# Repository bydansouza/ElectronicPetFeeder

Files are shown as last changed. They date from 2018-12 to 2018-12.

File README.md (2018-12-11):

# About this! 
Electronic Pet Feeder Project - Automatic Feeder for Dogs and Cats ;)

By Daniel Henrique Camargo de Souza @ PIN22107 - IFSC/Electronic Engineering/Professors: Daniel Lohmann AND Robinson Pizzio - Dezembro/2018

# Descript:

This project consists of an electronic automatic feeder for dogs and cats, and this project were made from course Integrator Project class in undergraduate at Electronic Engineering by IFSC/Florianópolis@Brazil.

# Guide to using this repository folders and files
Here you find this structure of folders and files

* `CODE` contains the main code, the Makefile and includes for compile code to microcontroller ESP8266. 

* `ELECTRONIC_DESIGN` contains the files for electronic scheme and PCB design of the circuit for the control system.

* `MECHANICAL_DESIGN` contain the files of mechanical part, essentially the helicoid part design, other parts were made from commercials items.

* `_guides` contain files for learning about sensor and controllers used in this project, essentially datasheets and manuals

* `_models` contain files for other electronic pet feeder, but this was made with Arduino (sic) 

* `_patents` contain files of patents discovered about electronic pet feeders.

* `_refs` Others references files

# Steps for sucess:

* 1) Market research:

** First we proceded in a market research, seeking out a similar product. **

List of similar products:

   [10 Best Automatic Pet Feeders 2017](https://www.youtube.com/watch?v=MUnrIJn3qq8)

   [10 Best Automatic Pet Feeders 2018](https://www.youtube.com/watch?v=D8cHpOWlC1c)

   [JEMPET Petwant SmartFeeder Automatic Pet Feeder](http://www.petwant.com/)
    
   [Automatic Cat Feeder | PF-10 CAT](https://www.petfeedster.com/product/automatic-cat-feeder/)
        
** in following, we search the prices of these similar products **
    
   [JEMPET Petwant SmartFeeder Automatic Pet Feeder](https://www.amazon.com/Petwant-SmartFeeder-Automatic-Dispenser-Controlled/dp/B01GFTZPDQ)
    
   [Smart Feed Automatic Pet Feeder](https://store.petsafe.net/smart-feed)
    
   [Automatic Cat Feeder | PF-10 CAT](https://www.amazon.com/New-Pet-Feedster-PF-10-PLUS/dp/B01N9D4672)

* 2) Diferenciais Attributes for this project:

    All configs via MQTT
    
    Notification for user 
    
    Water control, Temperature and level

# Mechanical Project

This project is a prototype, then we use PVC commercial tubes of the 100mm to make mechanical part. however, for helicoidal transport of feed, we maked (via freecad) a design of the helicoid and built it via 3D printer. this part design you can see in folder `MECHANICAL_DESIGN`
    
We inspired from [Helidoid Model](https://www.thingiverse.com/thing:27854) to construct the helicoid part. This is inside into PVC tube of the 100mm of format "T". in the base of the helicoid have a motor that spin this helicoid liberating the feed.

The Helicoid design part coudl be seen in the next image. 
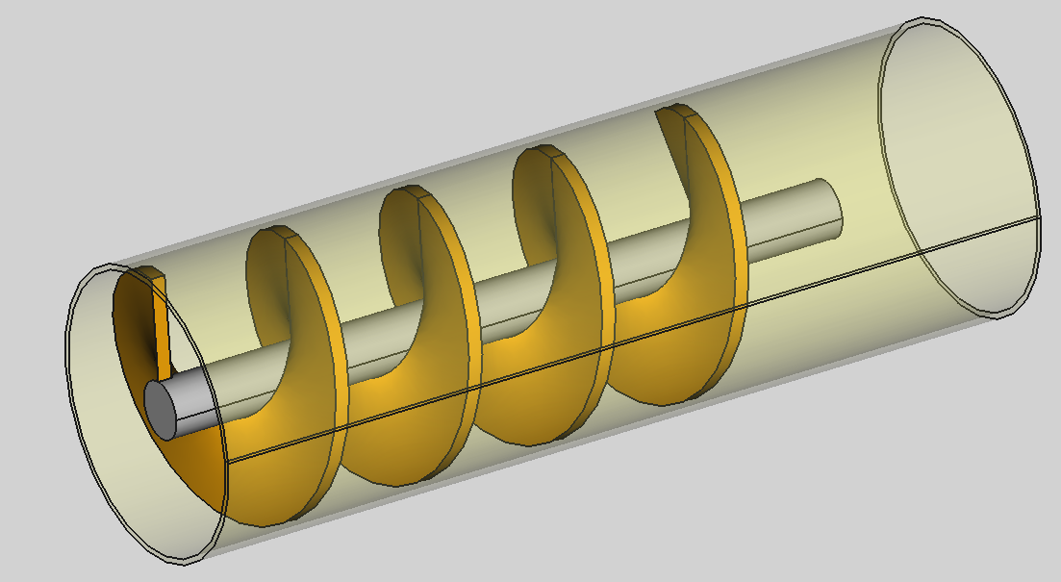
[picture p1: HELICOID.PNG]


The feed fall into the pot and under it (in the base) have a load cell for 2Kg, controlled from MCU (ESP8266). The client set, with MQTT commands, a quantity of feed and the system control the motor to spin the necessary to liberate a quantity seted.

In the base of system, have too another load cell, of the 50Kg, that monitoring the quantity of feed that fall into the pot (exited of system load). inside in code have a routine that calculate the variation of load, that fall into the pot and exited of system load, this two quantities should are equals.

For monitoring and control the water input and output, have been installed two solenoid valves. Inside the water pot have a temperature sensor and level sensor that through MCU controller we monitoring this two variables, and controled the start or stop of solenoids valves (if necessary).

# Electronic Project

Let's go to the part that interest us. For the control system, we used a microcontroller ESP8266 because it contain various periferics integrated, example is Wi-Fi Module.

Together of the MCU microcontroller, we used two accessories periferics. The first is HX711, Load cell controller that communicate with MCU part trough two pins serial interface, we implemented the librarie for this communicate with ESP8266 (see you into `CODE`). The second is RTC (Real Time Controller) based in DS1307, this is used in control of the time, and for this we used the librarie avaiable in `esp-open-rtos`

For the water temperature control, we used the DS18B20 Sensor (because this is water resistant), then for communicate with MCU microcontroller this sensor use one wire communication, and this is implemented in the librarie included in `esp-open-rtos`.

In the water level control, we used a capacitive sensor connected in input of 555 oscillator. according that the level rises, the oscillation produced in 555 change, the capacitive sensor controll the frequency of the oscillation in 555, thus we have a converter of the water level in frequency of oscilation. the second stage is connect the output os the 555 in an VCO (Voltage Control Oscilator) configured to convert frequency oscilations in voltages levels, thus we have the complete cicle, and we connect this output voltage level in an analog to digital converter of the MCU Controller.

The PCB design could be seen in the next image.  
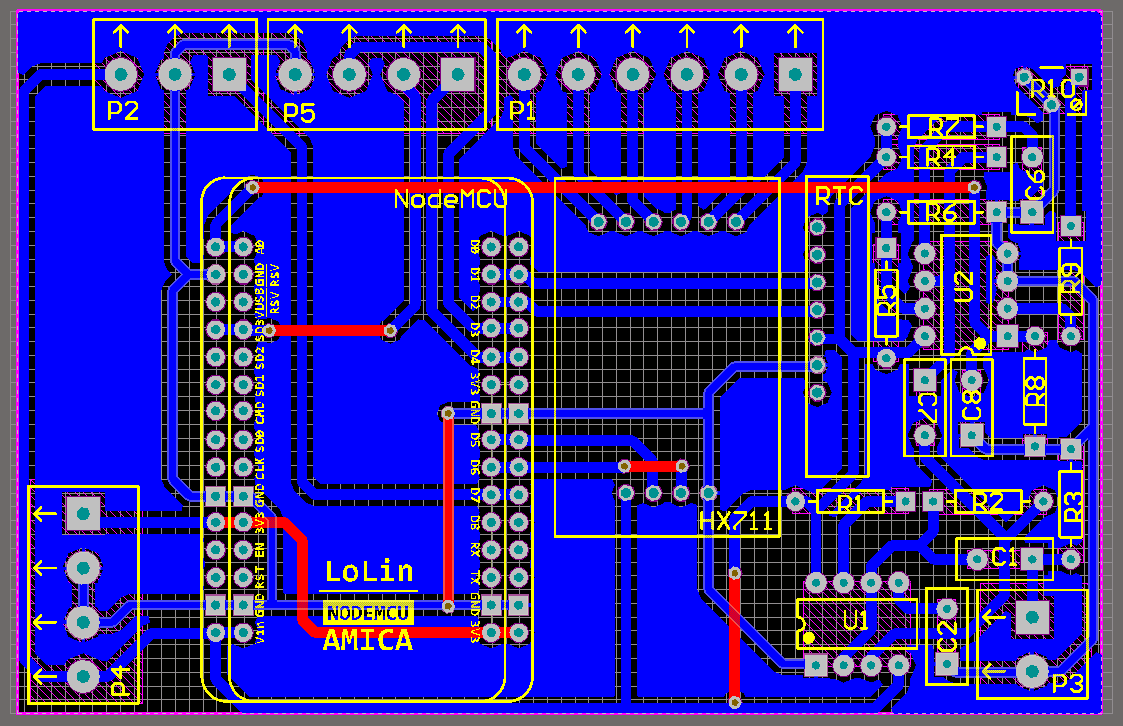
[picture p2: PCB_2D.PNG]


In this design we priorise the final dimension of board and the disposition os the components in board for reduce EMI an another other possibles mistakes.

The 3D PCB design could be seen in the next image. 
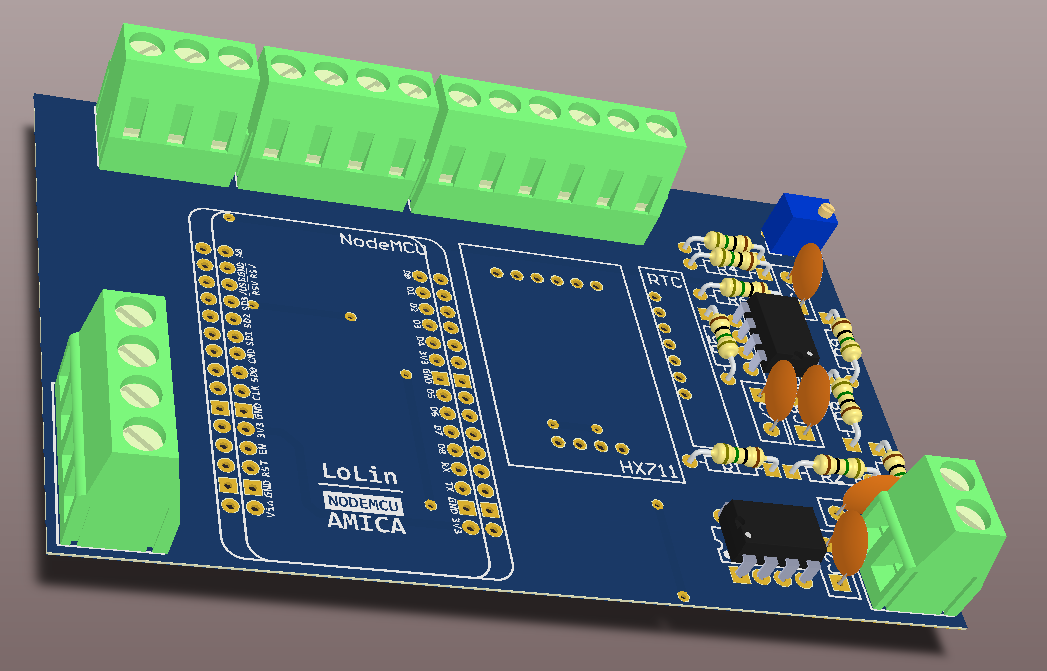
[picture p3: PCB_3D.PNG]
PCB 3D


## Main Code

The main code was made with esp-open-rtos sdk to ESP8266, then recommended to use the [esp-open-rtos](https://github.com/SuperHouse/esp-open-rtos). after defines, we created a sctruc that contain the principals control variables and the principals flags for control system, see next.

```
typedef struct {
	union
	{
		struct
		{
			uint32_t fIsTime		: 1;	//Chegou a Hora da Dose
			uint32_t fEqualDose		: 1;	//Dose Igualou
			uint32_t fMotorDose		: 1;	//Start/Stop do Motor da Dose
			uint32_t fWaterLevel	: 1;	//Chegou no Nível de Agua
			uint32_t fWaterTemp		: 1;	//Temperatura Ultrapassou
			uint32_t fWaterInput	: 1;	//Start/Stop entrada de agua
			uint32_t fWaterOutput	: 1;	//Start/Stop Saída de agua
			uint32_t fUnusedBits	: 25;	//Flags não usadas (fUnusedBits+Others = 32bits)
		};
		uint32_t fAllFlags;					//All Flags
	}			feeder_flags;			//Flags de Controle
	uint8_t 	feeder_nDose;			//Numero de Doses Diárias programadas
	uint32_t 	feeder_min[NMAX_DOSE];	//Minutos das Doses programadas
	uint32_t 	feeder_hour[NMAX_DOSE];	//Horas das Doses programadas
	uint32_t 	feeder_mday;			//Marca o Dia, para não repetir horários
	uint32_t 	feeder_dose;			//Quatidade da Dose Programada
	uint32_t	feeder_delay;			//Delay para as demais Tarefas
	float 		feeder_waterTemp;		//Temperatura da Agua permitida
}petFeederControl_t;
```
For the mensures and controls, we create 11 tasks, you can see theses tasks in the main code in `CODE` folder. for MQTT publisher and subscrtibe routines we was made based in code produced by @xtarke avaiable [Here](https://github.com/xtarke/kairos/tree/master/codes/mqtt). 

# Others Projects
[Pet Feeder w/ Arduino](https://www.instructables.com/id/Automatic-Arduino-Powered-Pet-Feeder/)

[IoT Pet Feeder](https://www.hackster.io/circuito-io-team/iot-pet-feeder-10a4f3)

[Other Pet Feeder](https://www.circuito.io/blog/automatic-pet-feeder/)

[Other Pet Feeder w/ Arduino](https://circuitdigest.com/microcontroller-projects/automatic-pet-feeder-using-arduino)

[Other Mechanical Pet Feeder](https://www.youtube.com/watch?v=hpQ21NZ_fuw)

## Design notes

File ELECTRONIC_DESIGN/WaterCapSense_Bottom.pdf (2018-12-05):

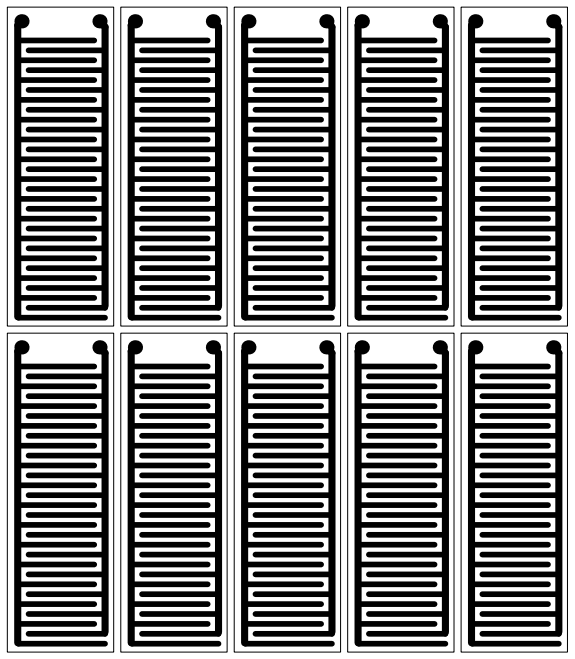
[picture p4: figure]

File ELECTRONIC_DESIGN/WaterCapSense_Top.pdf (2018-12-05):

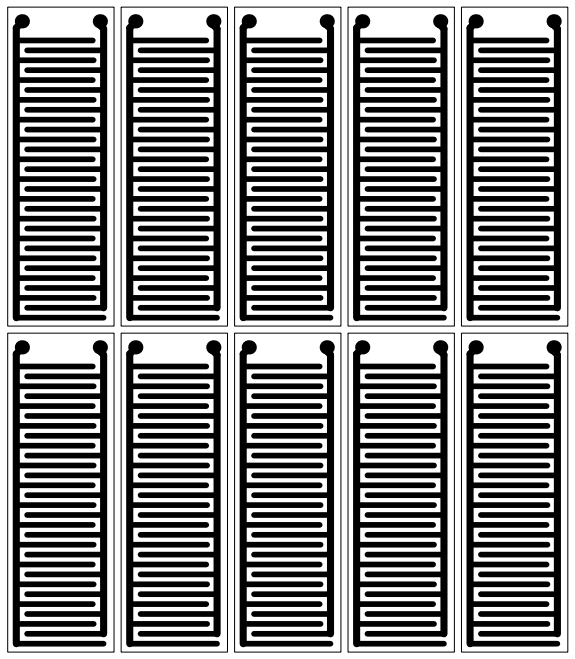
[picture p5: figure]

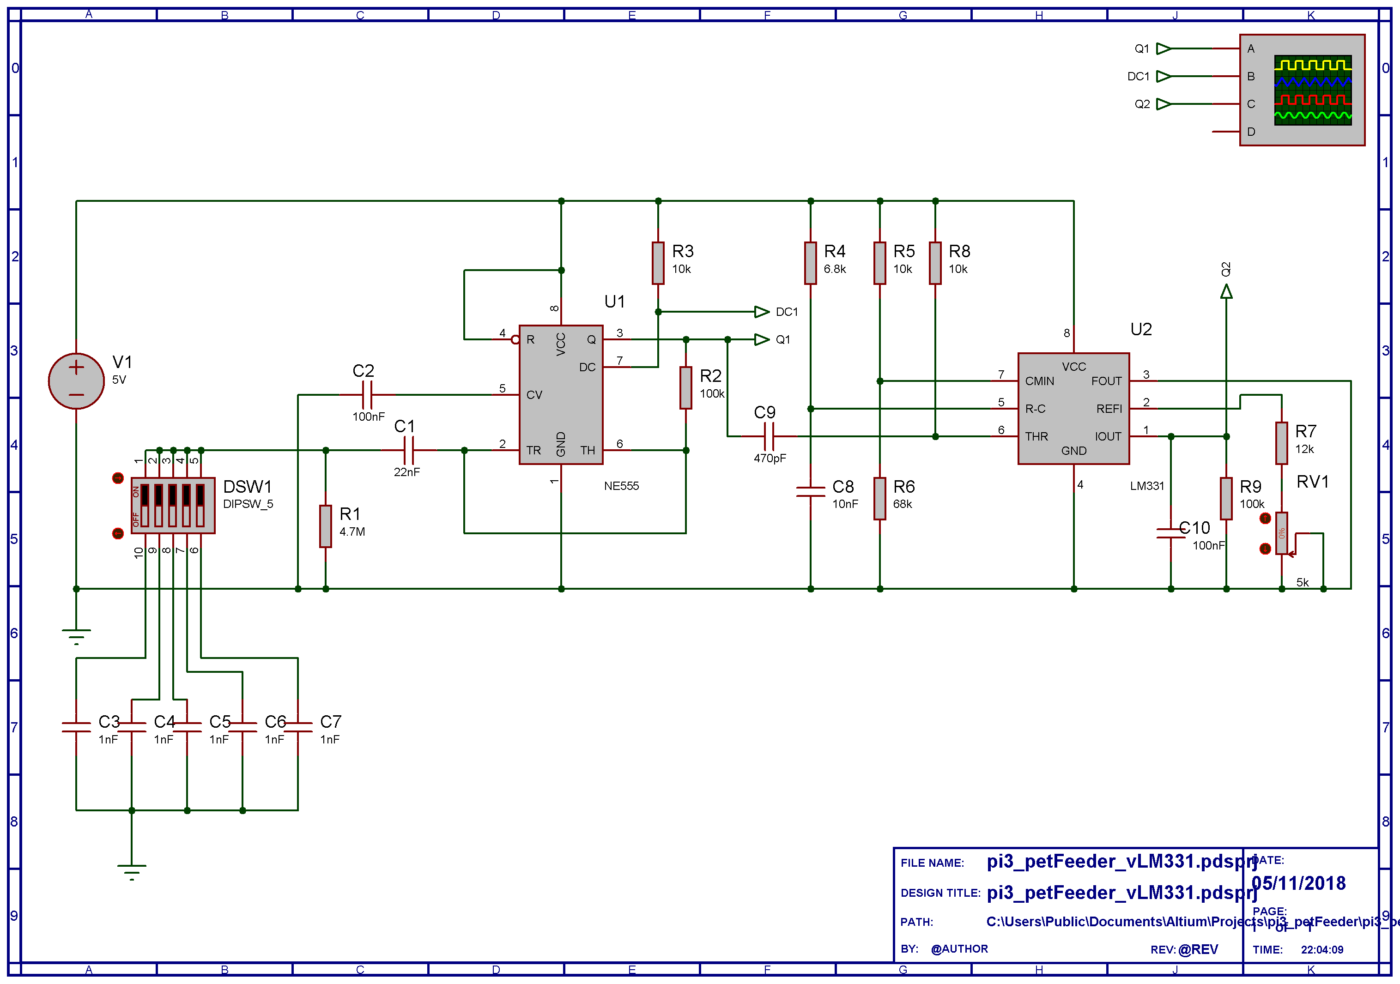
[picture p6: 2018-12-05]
ELECTRONIC_DESIGN/pi3_petFeeder_vLM331.png

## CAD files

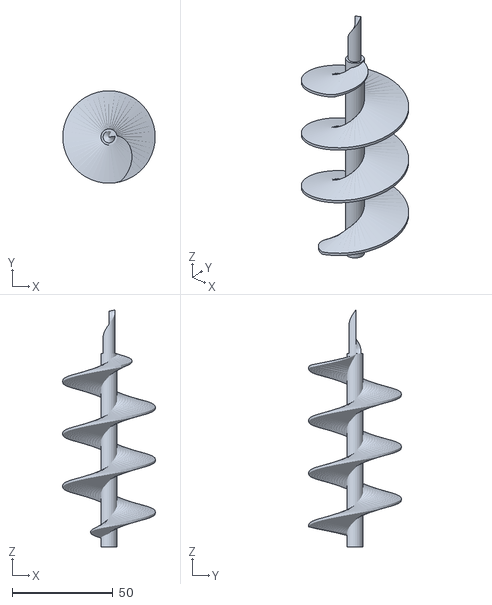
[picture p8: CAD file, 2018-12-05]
_models/Auger-based_Cat_Feeder/auger.stl
45.9 x 45.9 x 117.5

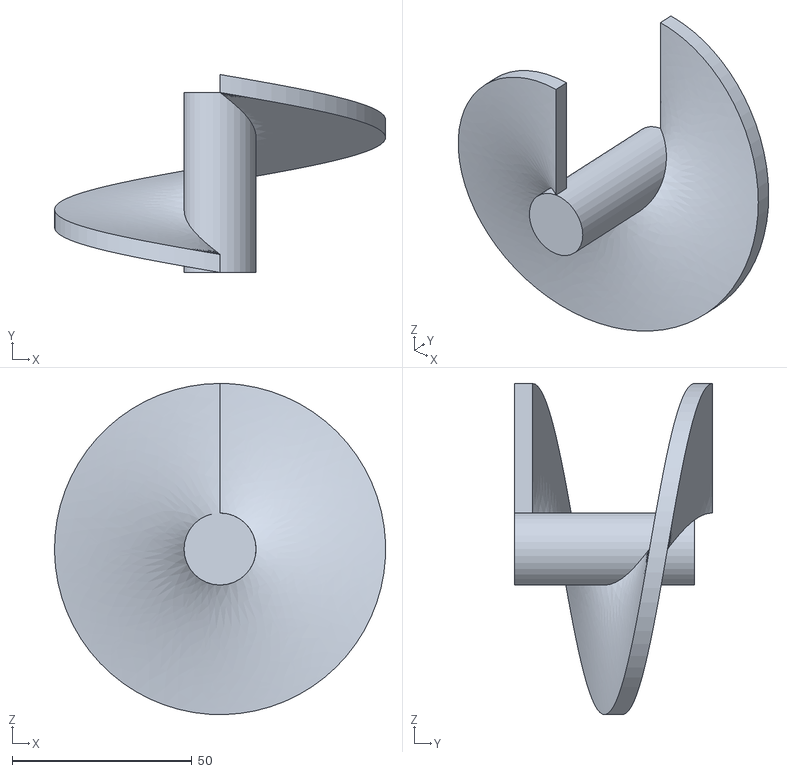
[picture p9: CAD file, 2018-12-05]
MECHANICAL_DESIGN/5x_helicoid_part001.stl
92.0 x 55.0 x 92.0

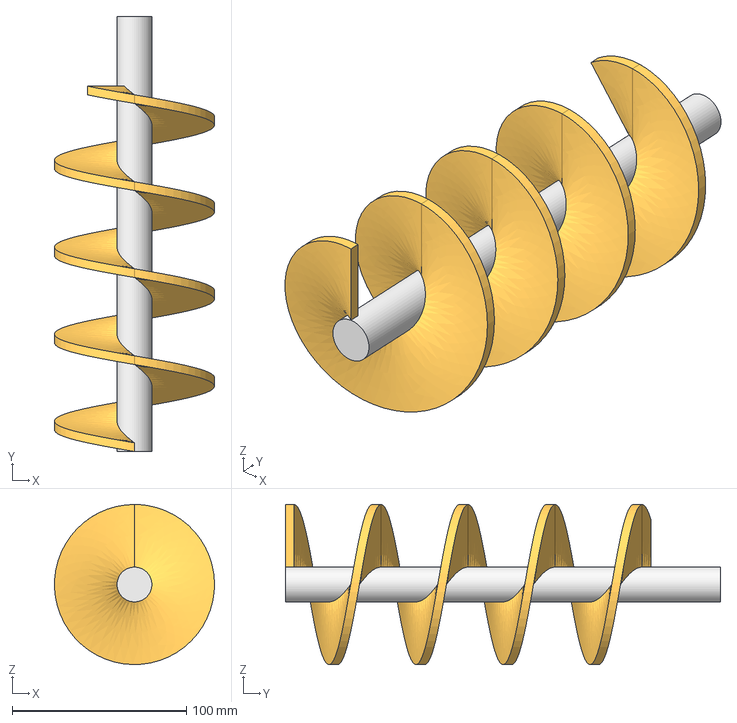
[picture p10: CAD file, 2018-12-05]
MECHANICAL_DESIGN/_helicoid.FCStd
91.9 x 250.0 x 92.0 mm
Eixo

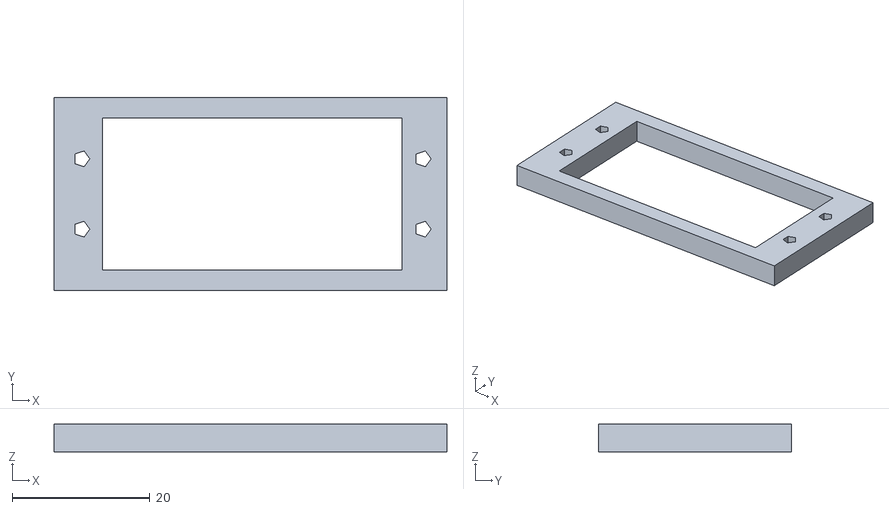
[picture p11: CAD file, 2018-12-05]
_models/Auger-based_Cat_Feeder/auger_servoshim.stl
57.0 x 28.0 x 4.00

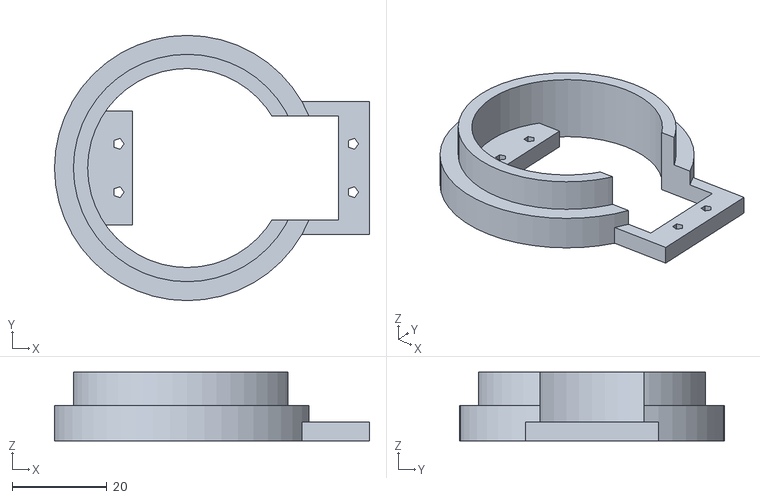
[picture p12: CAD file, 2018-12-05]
_models/Auger-based_Cat_Feeder/auger_tubemount.stl
66.5 x 56.0 x 14.5

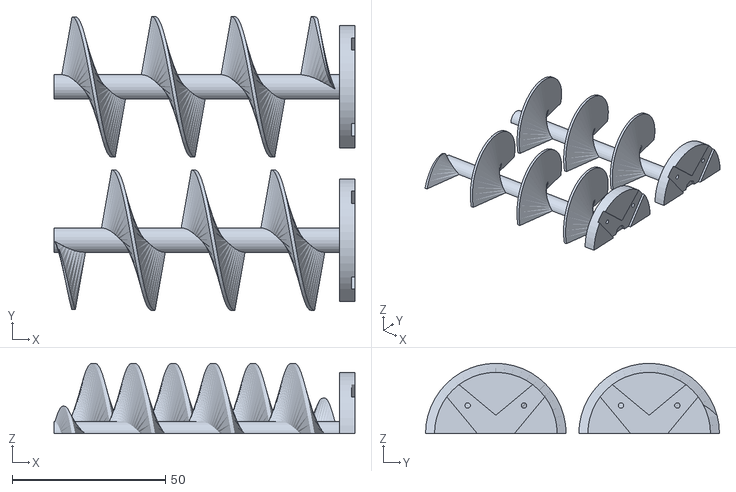
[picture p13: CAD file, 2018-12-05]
_models/Auger-based_Cat_Feeder/auger_screwplate.stl
98.0 x 95.9 x 22.9

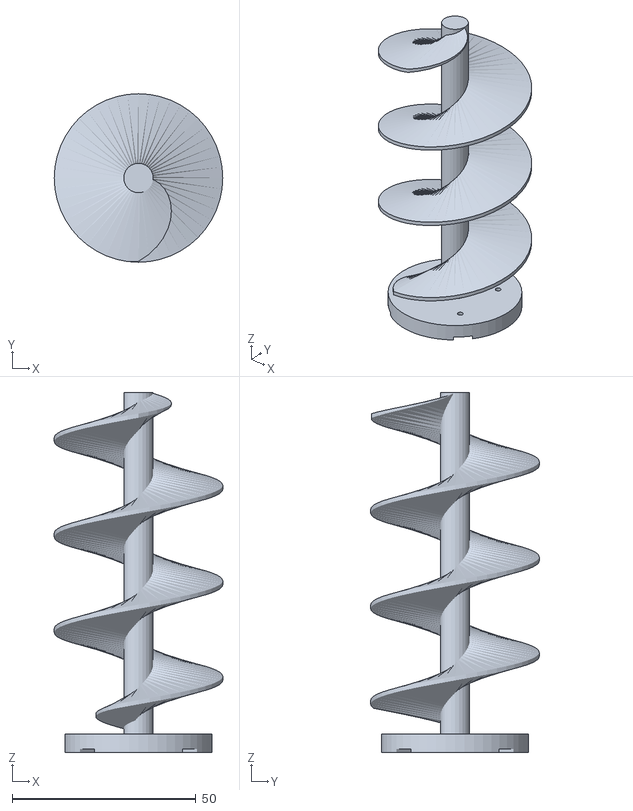
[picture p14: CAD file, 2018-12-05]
_models/Auger-based_Cat_Feeder/auger_screw.stl
45.9 x 45.9 x 98.0

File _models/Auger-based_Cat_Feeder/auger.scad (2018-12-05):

use <Thread_Library.scad>

// slice along Y-axis

*auger();
auger_import();

drivemount();

tubemount();

*servoshim();

%pvctube();

*servo();

module auger_import() {
    intersection() {
        translate([-45,-45,0]) cube(96);
        rotate([0,0,-15]) import("auger.stl");
    }
}
module auger() {
    cylinder(h=96, r=4, $fn=24);    
    trapezoidThread( 
        length=118,
        pitch=26,
        pitchRadius=8,
        threadHeightToPitch=0.70,
        profileRatio=0.20,
        threadAngle=10,
        RH=true,
        clearance=0.1,
        backlash=0.1,
        stepsPerTurn=48
    );
}

module drivemount() {
    translate([0,0,-2]) difference() {
        cylinder(h=5, r=40/2, $fn=48);
        for (angle = [0, 90, 180, 270]) translate([0,0,-1]) rotate([0,0,-45+angle]) {
            linear_extrude(height=2) polygon([[-8.5/2,0],[8.5/2,0],[8.5/2,8.5/2],[5.4/2,42/2],[-5.4/2,42/2],[-8.5/2,8.5/2]]);
            translate([13,0,0]) cylinder(h=8, r=0.9, $fn=12);  // 10 or 13
        }
        cylinder(h=2, r=3, $fn=8);
    }
}

module pvctube() {
    translate([0,0,-3]) difference() {
        cylinder(h=90, r=55/2, $fn=48);
        translate([0,0,-1]) cylinder(h=92, r=48/2, $fn=48);
    }
    // TODO: measure PVC tube and make sure these numbers make sense
}

module tubemount() {
    color([1,0,0])
    translate([0,0,-1-3]) difference() {
        union() {
            difference() {
                union() {
                    cylinder(h=3+5, r=48/2, $fn=48);
                    translate([0,0,-6.5]) cylinder(h=7.5, r=56/2, $fn=48);
                    translate([13,-22/2-3,-6.5]) cube([25.5,22+3*2,4]);
                }
                translate([0,0,-7]) cylinder(h=20, r=42/2, $fn=48);
                translate([0,-22/2,-19.5]) cube([32,22,20+10]);
            }
            translate([-21.5,-24/2,-6.5]) cube([10,24,4]);
        }
        translate([-4.5-10,-20.2/2,-11]) union() {
            translate([0,5,0]) cylinder(h=10, r=1.2);
            translate([0,5+10.2,0]) cylinder(h=10, r=1.2);
            translate([50.5-1,5,0]) cylinder(h=10, r=1.2);
            translate([50.5-1,5+10.2,0]) cylinder(h=10, r=1.2);
        }
    }
    // #2 x length? 2.0mm?  hole is ~1.55mm
}


module servoshim() {
    color([.7,.7,0])
    translate([0,0,-1-3-20]) difference() {
        union() {
            difference() {
                translate([-18.5,-22/2-3,-6.5]) cube([31.5+25.5,22+3*2,4]);
                translate([-18,-22/2,-19.5]) cube([18+32,22,20+10]);
            }
            translate([-18.5,-24/2,-6.5]) cube([7,24,4]);
        }
        translate([-4.5-10,-20.2/2,-11]) union() {
            translate([0,5,0]) cylinder(h=10, r=1.2);
            translate([0,5+10.2,0]) cylinder(h=10, r=1.2);
            translate([50.5-1,5,0]) cylinder(h=10, r=1.2);
            translate([50.5-1,5+10.2,0]) cylinder(h=10, r=1.2);
        }
    }
}




module servo() {
    color([0,0.7,.3])
    translate([-4.5-10,-20.2/2,-12-3]) union() {
        cube([50.5,20.2,4.5]);
        translate([4.5,0,0]) cube([41.5,20.2,11]);
        translate([4.5+10,20.2/2,11]) cylinder(h=4, r=3, $fn=24);
        translate([0+1,5,0]) cylinder(h=10, r=1);
        translate([0+1,5+10.2,0]) cylinder(h=10, r=1);
        translate([50.5-1,5,0]) cylinder(h=10, r=1);
        translate([50.5-1,5+10.2,0]) cylinder(h=10, r=1);
    }
}

// TODO: T-junction tube?  Or drill hole in top?
// TODO: diagonal mount to the bin?

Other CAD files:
MECHANICAL_DESIGN/_helicoid_part01.FCStd
_models/Auger-based_Cat_Feeder/augerslice.scad
_models/Auger-based_Cat_Feeder/Thread_Library.scad
MECHANICAL_DESIGN/helicoid.stl

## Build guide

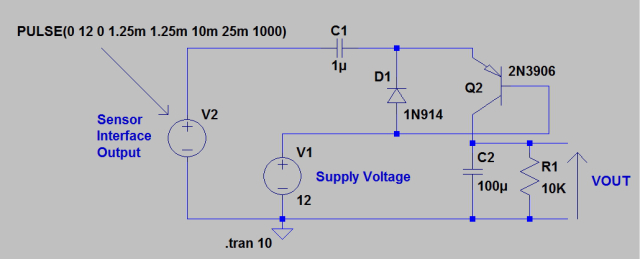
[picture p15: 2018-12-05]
_guides/waterLevelCapacitive/v2f.jpg

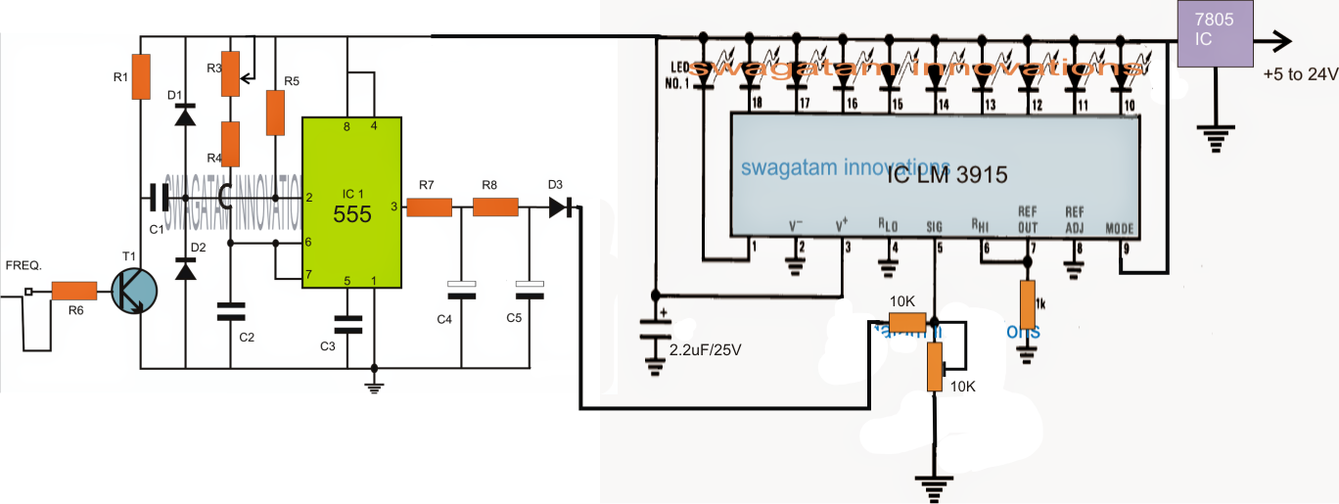
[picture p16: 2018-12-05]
_guides/waterLevelCapacitive/main-qimg-3cc157e7e807a82d9649140c95fcf219.png

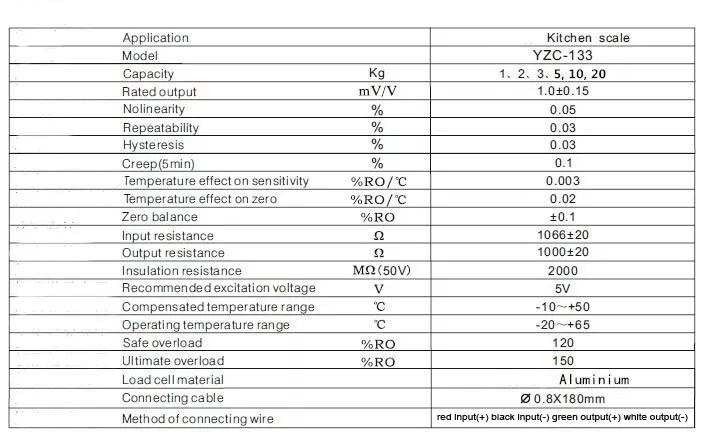
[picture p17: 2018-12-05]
_guides/hx711/celula-de-carga-2kg-sensor-de-peso-arduino-0213-D_NQ_NP_987008-MLB26000520462_092017-F.webp

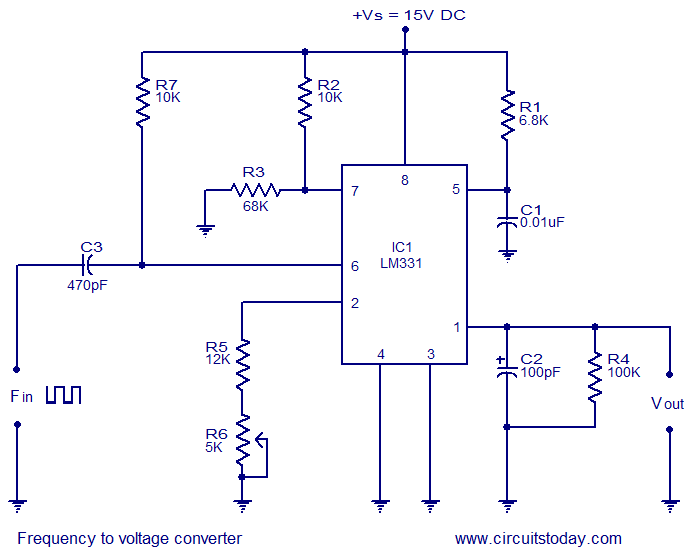
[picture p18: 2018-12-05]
_guides/waterLevelCapacitive/Frequency-to-Voltage-Converter.png

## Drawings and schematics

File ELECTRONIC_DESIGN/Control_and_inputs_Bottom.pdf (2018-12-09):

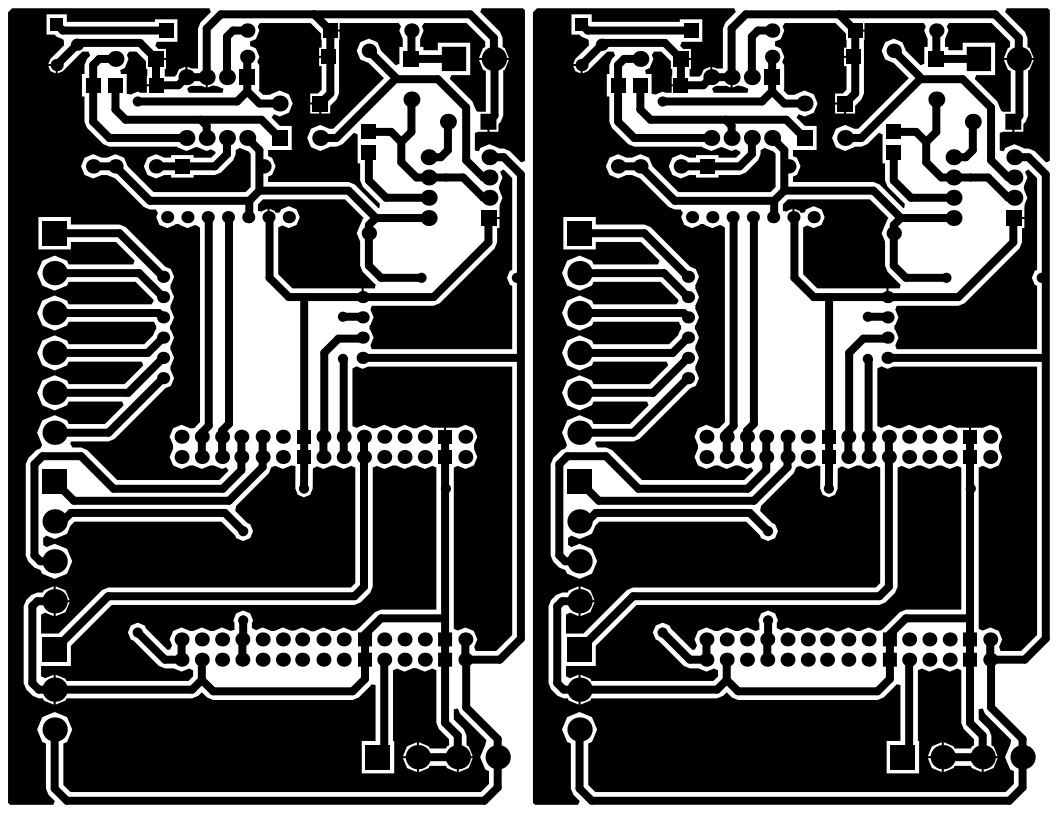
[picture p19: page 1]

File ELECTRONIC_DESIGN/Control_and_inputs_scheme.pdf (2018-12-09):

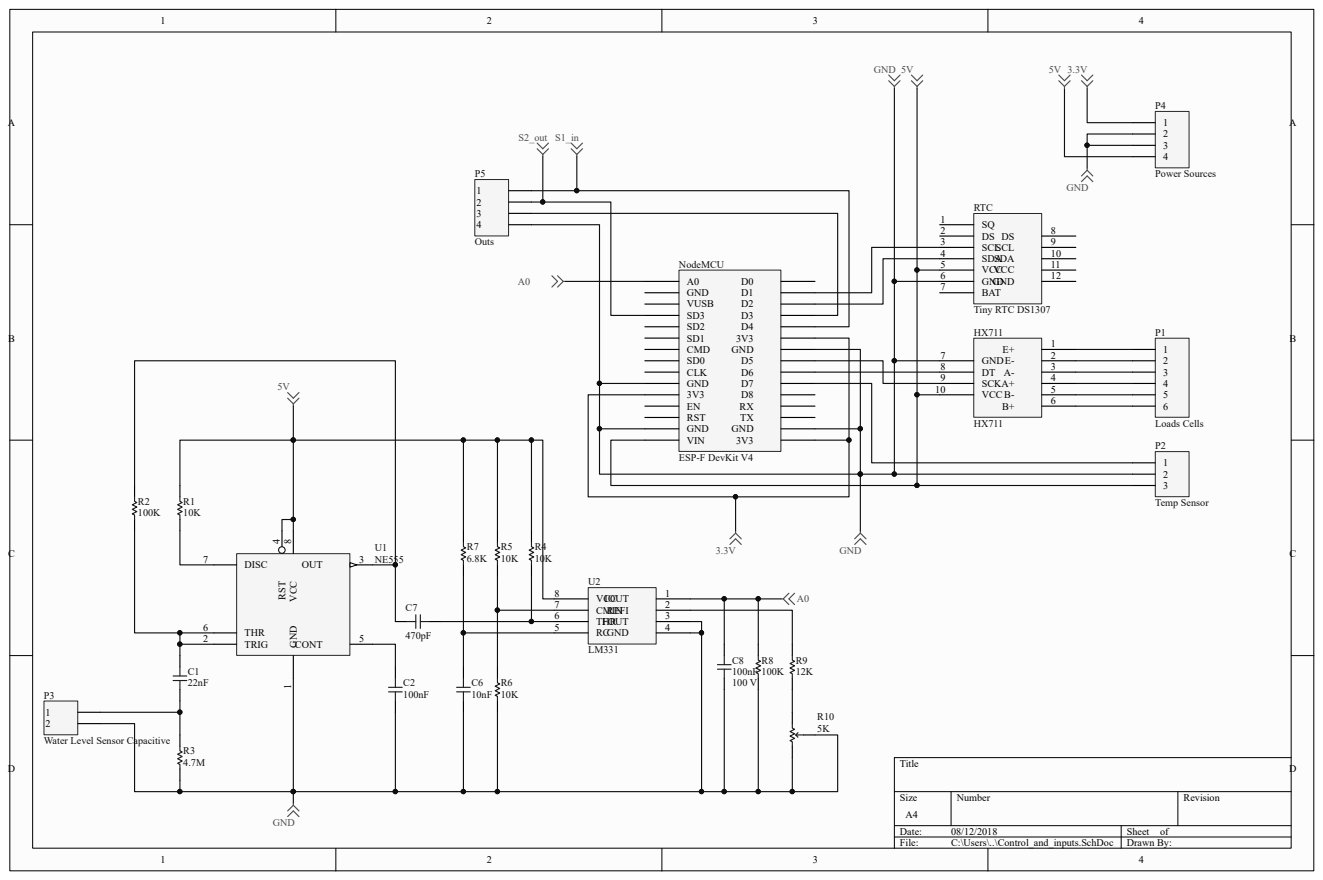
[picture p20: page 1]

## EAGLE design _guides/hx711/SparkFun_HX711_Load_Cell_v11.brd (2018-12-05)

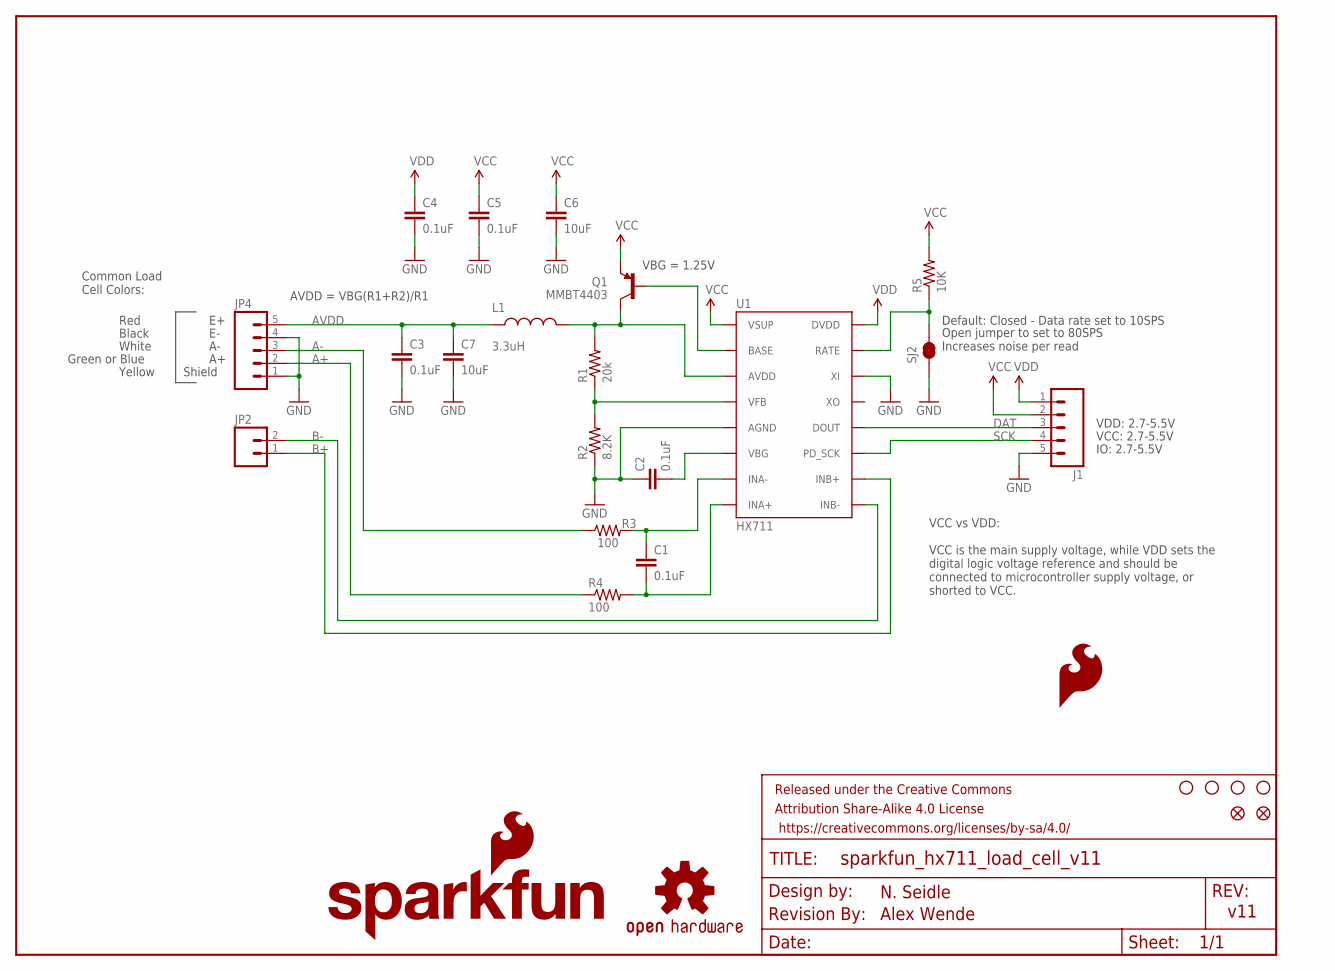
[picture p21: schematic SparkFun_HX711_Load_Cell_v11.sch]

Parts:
C1, C2, C3, C4, C5: 0.1uF; 0603-CAP
C6, C7: 10uF; 1210
FID1, FID2: FIDUCIAL1X2; FIDUCIAL-1X2
FRAME1: FRAME-LETTER; CREATIVE_COMMONS
J1: M05PTH; 1X05
JP2: M02PTH; 1X02
JP4: M05PTH; 1X05
L1: 3.3uH; 0805
LOGO1: SFE_LOGO_NAME_FLAME.1_INCH; SFE_LOGO_NAME_FLAME_.1
LOGO3: SFE_LOGO_FLAME.1_INCH; SFE_LOGO_FLAME_.1
Q1: MMBT4403; SOT23-3
R1: 20k; 0603-RES
R2: 8.2K; 0603-RES
R3, R4: 100; 0603-RES
R5: 10K; 0603-RES
SJ2: JUMPER-PAD-2-NC_BY_TRACE; PAD-JUMPER-2-NC_BY_TRACE_YES_SILK
STANDOFF1, STANDOFF2, STANDOFF3, STANDOFF4: STAND-OFF
U1: HX711; SO16
U7: OSHW-LOGOS; OSHW-LOGO-S
U$1: REVISION

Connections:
A+: JP4.2, R4.1
A-: JP4.3, R3.1
AVDD: C3.1, C7.1, JP4.5, L1.1
B+: JP2.1, U1.10 (INB+)
B-: JP2.2, U1.9 (INB-)
DAT: J1.3, U1.12 (DOUT)
GND: C2.1, C3.2, C4.2, C5.2, C6.2, C7.2, J1.5, JP4.1, JP4.4, R2.1, SJ2.1, U1.5 (AGND), U1.14 (XI)
unnamed: R5.1, SJ2.2, U1.15 (RATE)
unnamed: C1.1, R3.2, U1.7 (INA-)
unnamed: C1.2, R4.2, U1.8 (INA+)
unnamed: Q1.1 (B), U1.2 (BASE)
unnamed: L1.2, Q1.3 (C), R1.2, U1.3 (AVDD)
unnamed: R1.1, R2.2, U1.4 (VFB)
unnamed: C2.2, U1.6 (VBG)
SCK: J1.4, U1.11 (PD_SCK)
VCC: C5.1, C6.1, J1.2, Q1.2 (E), R5.2, U1.1 (VSUP)
VDD: C4.1, J1.1, U1.16 (DVDD)

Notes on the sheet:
VCC: 2.7-5.5V
VBG = 1.25V
AVDD = VBG(R1+R2)/R1
Default: Closed - Data rate set to 10SPS
Open jumper to set to 80SPS Increases noise per read
Red
Black
White
Green or Blue
Common Load Cell Colors:
IO: 2.7-5.5V
Shield
Yellow
VDD: 2.7-5.5V
VCC vs VDD: VCC is the main supply voltage, while VDD sets the digital logic voltage reference and should be connected to microcontroller supply voltage, or shorted to VCC.
Alex Wende
N. Seidle
v11

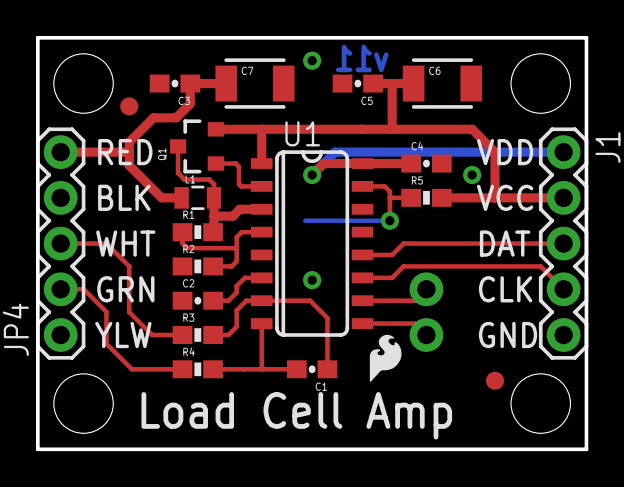
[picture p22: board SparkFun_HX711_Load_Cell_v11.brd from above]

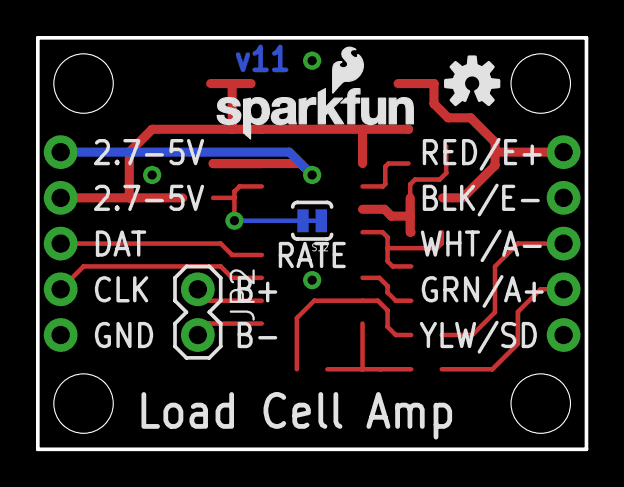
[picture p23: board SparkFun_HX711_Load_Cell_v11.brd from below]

Board: 2 copper layers, 30.5 x 22.9 mm, 30 parts (4 on the bottom side), 17 nets.

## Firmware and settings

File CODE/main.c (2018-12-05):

/*
 * main.c
 *	Main code to pi3 project in Electronic Engineering undergraduate Course at IFSC/Florianópolis-SC@Brasil
 *
 *      Author: Daniel Henrique Camargo de Souza, @byDansouza
 *
 *      Colaboration: xtarke (Prof:. Renan Starke)
 */
// Header files ----------------------------------------------------------------
#include "espressif/esp_common.h"
#include "esp/uart.h"

#include <string.h>

#include <FreeRTOS.h>
#include <task.h>
#include <ssid_config.h>

#include "esp8266.h"
#include "timers.h"
#include <queue.h>
#include <semphr.h>
#include "lwip/api.h"

#include <espressif/esp_sta.h>
#include <espressif/esp_wifi.h>
#include <paho_mqtt_c/MQTTESP8266.h>
#include <paho_mqtt_c/MQTTClient.h>
#include <paho_mqtt_c/MQTTSubscribe.h>

//Drivers Headers Files
#include "myincludes/ds18b20.h"		//Temperature Sensor
#include "myincludes/hx711.h"		//Load Cell amplifier
#include "myincludes/i2c.h"			//i2c Driver to RTC DS1307
#include "myincludes/ds1307.h"		//RTC DS1307 Driver
#include "myincludes/pwm.h"			//PWM Driver

#include "myincludes/network.h"
#include "myincludes/comm.h"
#include <sysparam.h>
#include "myincludes/app_status.h"

//Definitions
#include "myincludes/defPrincipais.h"

#define SENSOR_GPIO 13			//Temperature PIN Sensor
#define MAX_SENSORS 1			//Numbers of Temperatura Sensor in system
#define RESCAN_INTERVAL 1		//Scans in each sensor
#define LOOP_DELAY_MS 5000		//Temperature contain high inertia value, then the delay time can high

#define DOUT 12					//hx711 pin DOUT
#define PD_SCK 14				//hx711 pin PDSCK

#define I2C_BUS 1				//I2C Bus
#define SCL_PIN 5				//SCL I2C PIN
#define SDA_PIN 4				//SDA I2C PIN

#define MOTOR_PIN 0				//Motor PIN
#define WINPUT_PIN 2			//Water Input valve PIN
#define WOUTPUT_PIN 10			//Water Output valve PIN

#define WATER_SENSOR 15			//Capacitive Water Sensor PIN

//Initial Params For tests
#define NMAX_DOSE 6				//Numero máximo de doses diárias
#define DOSE_RACAO 30
#define DOSE_MIN 1
#define DOSE_HOUR 12
#define DELAY_TASKS 60000

static QueueHandle_t tsqueue;
static SemaphoreHandle_t xBinaryControl;

typedef enum petfeecomm_t{
	SET_NDOSE,
	SET_DOSE,
	SET_HOUR,
	SET_MIN,
	SET_WTEMP
}petfeecomm_t;

typedef struct {
	union
	{
		struct
		{
			uint32_t fIsTime		: 1;	//Chegou a Hora da Dose
			uint32_t fEqualDose		: 1;	//Dose Igualou
			uint32_t fMotorDose		: 1;	//Start/Stop do Motor da Dose
			uint32_t fWaterLevel	: 1;	//Chegou no Nível de Agua
			uint32_t fWaterTemp		: 1;	//Temperatura Ultrapassou
			uint32_t fWaterInput	: 1;	//Start/Stop entrada de agua
			uint32_t fWaterOutput	: 1;	//Start/Stop Saída de agua
			uint32_t fUnusedBits	: 25;	//Flags não usadas (fUnusedBits+Others = 32bits)
		};
		uint32_t fAllFlags;					//All Flags
	}			feeder_flags;			//Flags de Controle
	uint8_t 	feeder_nDose;			//Numero de Doses Diárias programadas
	uint32_t 	feeder_min[NMAX_DOSE];	//Minutos das Doses programadas
	uint32_t 	feeder_hour[NMAX_DOSE];	//Horas das Doses programadas
	uint32_t 	feeder_mday;			//Marca o Dia, para não repetir horários
	uint32_t 	feeder_dose;			//Quatidade da Dose Programada
	uint32_t	feeder_delay;			//Delay para as demais Tarefas
	float 		feeder_waterTemp;		//Temperatura da Agua permitida
}petFeederControl_t;
static petFeederControl_t petFeederControl;		//Create Static Global Variable

#define DEBUG

#ifdef DEBUG
#define debug(fmt, ...) printf("%s: " fmt "\n", "DEBUG", ## __VA_ARGS__)
#else
#define debug(fmt, ...)
#endif

static void  status_publish_task(void *pvParameters){
	uint8_t count = 0;
	TickType_t xLastWakeTime = xTaskGetTickCount();

    publisher_data_t to_publish;

    char *wifi_my_host_name = NULL;

	/* Get MQTT host IP from web server configuration */
	sysparam_get_string("hostname", &wifi_my_host_name);

	if (!wifi_my_host_name){
		printf("Invalid host name\n");
		strncpy(to_publish.topic,"host_1/heartbeat",PUB_TPC_LEN);
	}else{
		strncpy(to_publish.topic, wifi_my_host_name,PUB_TPC_LEN);
		free(wifi_my_host_name);
		strncat(to_publish.topic,"/heartbeat",PUB_TPC_LEN);
	}

    while (1) {
        vTaskDelayUntil(&xLastWakeTime, 1000 / portTICK_PERIOD_MS);

        //temperature = get_temperature();

        snprintf(to_publish.data, PUB_MSG_LEN, "Beat %d\r\n", count++);

        if (xQueueSend(publish_queue, (void *)&to_publish, 0) == pdFALSE) {
        	debug("Publish queue overflow.\r\n");
        }
    }
}

static void  status_subscrib_task(void *pvParameters){
    int size;
    uint8_t incH,i;
	command_data_t rx_data;

    while(1){
        while(xQueueReceive(command_queue, (void *)&rx_data, (TickType_t)10000) == pdTRUE){
            debug("Command: %d\n",rx_data.cmd);
            debug("Data: %lu\n",rx_data.data);

            switch (rx_data.cmd){
				case SET_NDOSE:
					petFeederControl.feeder_nDose = (uint8_t)rx_data.data;
					incH = petFeederControl.feeder_nDose/18;				//18 horas uteis para tratar animais
					break;
				case SET_DOSE:
					petFeederControl.feeder_dose = rx_data.data/petFeederControl.feeder_nDose;		//Dose Diaria / Numero de Doses no dia
					break;
				case SET_HOUR:
					petFeederControl.feeder_hour[0] = rx_data.data;
					for(i=1;i<petFeederControl.feeder_nDose;i++){
						petFeederControl.feeder_hour[i] = petFeederControl.feeder_hour[i-1]+incH;		// Set demais horarios
					}
					break;
				case SET_MIN:
					for(i=0;i<petFeederControl.feeder_nDose;i++){
						petFeederControl.feeder_min[i] = rx_data.data;
					}
					break;
				case SET_WTEMP:
					petFeederControl.feeder_waterTemp = (float)rx_data.data;
					break;
            }
        }
    }
}

void gpio_intr_handler(){
    uint32_t now = xTaskGetTickCountFromISR();
    xQueueSendFromISR(tsqueue, &now, NULL);
}

void mensure_waterlevel(void *pvParameters){
    gpio_enable(WATER_SENSOR, GPIO_INPUT);
	gpio_set_interrupt(WATER_SENSOR, GPIO_INTTYPE_EDGE_NEG, gpio_intr_handler);
    uint32_t period;
    uint32_t last = 0;

    while(1) {
    	xQueueReceive(tsqueue, &period, (TickType_t)100 );

        if(last < period) {

        	debug("\t\t\tPeriod is %d[ms]\r\n", (period-last)*portTICK_PERIOD_MS);

        	//IMPLEMENTAR O NÍVEL DE AGUA		02/12/2018

            last = period;
        }
    }
}

void realtime_task(void *pvParameters){
	uint8_t i;
	i2c_init(I2C_BUS, SCL_PIN, SDA_PIN, I2C_FREQ_400K);

	i2c_dev_t dev = {
		.addr = DS1307_ADDR,
	    .bus = I2C_BUS,
	};

	// setup datetime: 2016-11-1 12:00:01
	struct tm time = {
		.tm_year = 2018,
	    .tm_mon  = 11,  // 0-based
	    .tm_mday = 1,
	    .tm_hour = 12,
	    .tm_min  = 00,
	    .tm_sec  = 01
	};

	ds1307_start(&dev, TRUE);

	if (ds1307_is_running(&dev)){
		ds1307_set_time(&dev, &time);
	}else{
		ds1307_start(&dev, TRUE);
	}

	while(1){
		ds1307_get_time(&dev, &time);

		debug("\t%04d-%02d-%02d %02d:%02d:%02d\n", time.tm_year, time.tm_mon + 1, time.tm_mday, time.tm_hour, time.tm_min, time.tm_sec);

		//Comparar Horario (Minuto e Hora) com setado
		for(i=0;i<petFeederControl.feeder_nDose;i++){
			if (time.tm_min == petFeederControl.feeder_min[i] && time.tm_hour == petFeederControl.feeder_hour[i]){
					petFeederControl.feeder_flags.fIsTime = TRUE;			//Chegou a Hora da Ração
					petFeederControl.feeder_delay = 100;					//Deixa Todas as Tasks em ALERTA
			}else{
				petFeederControl.feeder_flags.fIsTime = FALSE;
			}
		}
		vTaskDelay(DELAY_TASKS/portTICK_PERIOD_MS); //wait 1min
	}
}

void mensure_loadcell(void *pvParameters){
	uint32_t _dose;
	uint32_t _racao;

	hx711_instance_t* _feeder = new_hx711(DOUT,PD_SCK,G64,CHANNEL_A);
	hx711_instance_t* _pot = new_hx711(DOUT,PD_SCK,G32,CHANNEL_B);

	while(1){
		prepare_channel(_pot); 						//Prepare channel and gain -- setting pulse numbers
		_dose = readhx711(_pot)&0xFFFFFB00;  		//Elimina os 10bits menos significativos
		if (_dose < 8427520) _dose = 8427520;		//Valor da Tara --> 8427520 (Medida em 02/11/2018)

		debug("Dose = %lu\n",convert_dose(_dose)/1000);	//Converte para miligramas(mg) e Divide por 1000 para fornecer em gramas (g)

		prepare_channel(_feeder);
		_racao = readhx711(_feeder)&0xFFFFFB00;  		//Elimina os 10bits menos significativos
		if (_racao < 8357888) _racao = 8357888;			//FALTA CALIBRAR A RACAO??? (28/11/2018)

		debug("\t\tRacao = %lu\n",convert_racao(_racao)/1000);

		if (convert_dose(_dose)/1000 > petFeederControl.feeder_dose){
			petFeederControl.feeder_flags.fEqualDose = TRUE;
		}else{
			petFeederControl.feeder_flags.fEqualDose = FALSE;
		}

		vTaskDelay(1000/portTICK_PERIOD_MS);
	}
}

void mensure_watertemp(void *pvParameters) {
    ds18b20_addr_t addrs[MAX_SENSORS];
    float temps[MAX_SENSORS];
    int sensor_count;

    // There is no special initialization required before using the ds18b20
    // routines.  However, we make sure that the internal pull-up resistor is
    // enabled on the GPIO pin so that one can connect up a sensor without
    // needing an external pull-up (Note: The internal (~47k) pull-ups of the
    // ESP8266 do appear to work, at least for simple setups (one or two sensors
    // connected with short leads), but do not technically meet the pull-up
    // requirements from the DS18B20 datasheet and may not always be reliable.
    // For a real application, a proper 4.7k external pull-up resistor is
    // recommended instead!)

    gpio_set_pullup(SENSOR_GPIO, TRUE, TRUE);

    while(1) {
        // Every RESCAN_INTERVAL samples, check to see if the sensors connected
        // to our bus have changed.
        sensor_count = ds18b20_scan_devices(SENSOR_GPIO, addrs, MAX_SENSORS);

        if (sensor_count < 1) {
			#ifdef DEBUG
            //printf("\nNo sensors detected!\n");
			#endif
        } else {
            //printf("\n%d sensors detected:\n", sensor_count);
            // If there were more sensors found than we have space to handle,
            // just report the first MAX_SENSORS..
            if (sensor_count > MAX_SENSORS) sensor_count = MAX_SENSORS;

            // Do a number of temperature samples, and print the results.
            for (int i = 0; i < RESCAN_INTERVAL; i++) {
                ds18b20_measure_and_read_multi(SENSOR_GPIO, addrs, sensor_count, temps);
                for (int j = 0; j < sensor_count; j++) {
                    // The DS18B20 address is a 64-bit integer, but newlib-nano
                    // printf does not support printing 64-bit values, so we
                    // split it up into two 32-bit integers and print them
                    // back-to-back to make it look like one big hex number.
                    uint32_t addr0 = addrs[j] >> 32;
                    uint32_t addr1 = addrs[j];
                    float temp_c = temps[j];
                    float temp_f = (temp_c * 1.8) + 32;

                    debug("Sensor %08x%08x reports: %f \xC2\xB0""C [%f \xC2\xB0""F] \n", addr0, addr1, temp_c, temp_f);

                    //FALTA IMPLEMENTAR UMA TEMPORIZAÇÃO -- Verificar se a temperatura se mantem assim por certo periodo de tempo (30min por exemplo)
                    // se sim... acionar o mecanismo de trca de agua
                    if(temp_c > petFeederControl.feeder_waterTemp){
                    	petFeederControl.feeder_flags.fWaterTemp = TRUE;		//Temperatura Ultrapassou
                    }else{
                    	petFeederControl.feeder_flags.fWaterTemp = FALSE;
                    }
                }

                // Wait for a little bit between each sample (note that the
                // ds18b20_measure_and_read_multi operation already takes at
                // least 750ms to run, so this is on top of that delay).
                vTaskDelay(LOOP_DELAY_MS / portTICK_PERIOD_MS);
            }
        }
    }
}

void control_motor(void *pvParameters) {
	gpio_enable(MOTOR_PIN, GPIO_OUTPUT);
	gpio_write(MOTOR_PIN,0);

	while(1){
		if(petFeederControl.feeder_flags.fMotorDose == TRUE){
			gpio_write(MOTOR_PIN,1);
			debug("Set MOTOR_PIN\n");

			if (petFeederControl.feeder_flags.fEqualDose == TRUE){
				gpio_write(MOTOR_PIN,0);
				debug("Reset MOTOR_PIN\n");

				petFeederControl.feeder_flags.fMotorDose = FALSE;
				petFeederControl.feeder_delay = DELAY_TASKS;
			}

			vTaskDelay(100/portTICK_PERIOD_MS);
		}else{
			gpio_write(MOTOR_PIN,0);
			vTaskDelay(petFeederControl.feeder_delay/portTICK_PERIOD_MS);
		}
	}
}

void control_waterinput(void *pvParameters) {
	gpio_enable(WINPUT_PIN, GPIO_OUTPUT);
	gpio_write(WINPUT_PIN,0);

	while(1){
		if(petFeederControl.feeder_flags.fWaterInput == TRUE){
			gpio_write(WINPUT_PIN,1);
			debug("Set WINPUT_PIN \n");

			if (petFeederControl.feeder_flags.fWaterLevel == TRUE){		//Nível de Agua = 1 (No Topo)
				gpio_write(WINPUT_PIN,0);
				debug("Reset WINPUT_PIN \n");

				petFeederControl.feeder_flags.fWaterInput = FALSE;
			}
			vTaskDelay(100/portTICK_PERIOD_MS);
		}else{
			gpio_write(WINPUT_PIN,0);
			vTaskDelay(petFeederControl.feeder_delay/portTICK_PERIOD_MS);
		}
	}
}

void control_wateroutput(void *pvParameters) {
	gpio_enable(WOUTPUT_PIN, GPIO_OUTPUT);
	gpio_write(WOUTPUT_PIN,0);

	while(1){
		if(petFeederControl.feeder_flags.fWaterOutput == TRUE){
			gpio_write(WOUTPUT_PIN,1);
			debug("Set WOUTPUT_PIN \n");

			if (petFeederControl.feeder_flags.fWaterLevel == FALSE){		//Nível de Agua = 0 (ZEROU)
				gpio_write(WOUTPUT_PIN,0);
				debug("Reset WOUTPUT_PIN \n");

				petFeederControl.feeder_flags.fWaterOutput = FALSE;
			}
			vTaskDelay(100/portTICK_PERIOD_MS);
		}else{
			gpio_write(WOUTPUT_PIN,0);
			vTaskDelay(petFeederControl.feeder_delay/portTICK_PERIOD_MS);
		}
	}
}

void control_FSM(void *pvParameters) {

	while(1){
		if(petFeederControl.feeder_flags.fIsTime == TRUE){
			petFeederControl.feeder_flags.fMotorDose = TRUE;
			debug("Is Time \n");
		}else{
			debug("No Time \n");

			petFeederControl.feeder_delay = DELAY_TASKS;
		}
		vTaskDelay(DELAY_TASKS/portTICK_PERIOD_MS);
	}
}

void user_init(void) {
    uart_set_baud(0, 115200);

    printf("SDK version:%s\n", sdk_system_get_sdk_version());

    // Set led to indicate wifi status.
    sdk_wifi_status_led_install(2, PERIPHS_IO_MUX_GPIO2_U, FUNC_GPIO2);

    xBinaryControl = xSemaphoreCreateBinary();
    xSemaphoreGive(xBinaryControl);					//Release the Semaphore

    petFeederControl.feeder_flags.fAllFlags = 0;
//    petFeederControl.feeder_dose = DOSE_RACAO;
//    petFeederControl.feeder_nDose = NMAX_DOSE;
//    petFeederControl.feeder_min[0] = DOSE_MIN;
//    petFeederControl.feeder_hour[0] = DOSE_HOUR;
    petFeederControl.feeder_delay = DELAY_TASKS;

    publish_queue = xQueueCreate(8, sizeof(publisher_data_t));
    command_queue = xQueueCreate(4, sizeof(command_data_t));
    tsqueue = xQueueCreate(2, sizeof(uint32_t));

    wifi_cfg();
    //trick by xtarke --> 'make erase_flash' to erase/renew flash memory of ESP8266

    xTaskCreate(&mensure_waterlevel, "WaterLevelMensure", 256, NULL, 2, NULL);
    xTaskCreate(&mensure_watertemp, "WaterTempMensure", 256, NULL, 2, NULL);
    xTaskCreate(&mensure_loadcell, "LoadCellMensure", 256, NULL, 2, NULL);
    xTaskCreate(&realtime_task, "DS1307", 256, NULL, 2, NULL);
    xTaskCreate(&control_motor, "MotorControl", 256, NULL, 2, NULL);
    xTaskCreate(&control_waterinput, "WinputControl", 256, NULL, 2, NULL);
    xTaskCreate(&control_wateroutput, "WoutputControl", 256, NULL, 2, NULL);
    xTaskCreate(&control_FSM, "FiniteStateMachine", 256, NULL, 2, NULL);

    xTaskCreate(&status_publish_task, "PublishComm", 256, NULL, 2, NULL);
    xTaskCreate(&status_subscrib_task, "SubscribComm", 256, NULL, 2, NULL);
    xTaskCreate(&mqtt_task, "mqtt_task", 1024, NULL, 7, NULL);

//Test MQTT
    // SUBSCRIVE to listen publish from PetFeeder Heatbeat
    // mosquitto_sub -v -h 172.16.0.2 -p 1883 -t eor-b27071/heartbeat

    // PUBLISH Command to PetFeeder
    // mosquitto_pub -m "1w0" -t eor-b27071/cfg/0
}

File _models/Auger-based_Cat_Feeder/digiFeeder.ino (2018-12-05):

//
//
// PIN-0 is connected to an active-low button
// (5V -- resistor -- GND -- button -- PIN0)
//
// PIN-1 is connected to an LED
// (GND -- (|<) -- PIN1)
//
// PIN-2 is connected to a servo
// (GND -- GND; 5V -- 5V; signal -- PIN2)
//
// digiSpark is driven via Vin, with a direction-limit diode, to 12V
//

#include <avr/pgmspace.h>

#define PIN_BTN 0  // manual trigger button
#define PIN_LED 1  // when-to-feed indicator
#define PIN_SRV 2  // servo

// human-linear scaled brightness, inverted (0-31)
const byte brightness[] PROGMEM = {
  255, 235, 216, 197, 180, 163, 148, 134,
  120, 108,  96,  86,  76,  67,  58,  51,
   44,  38,  32,  27,  22,  18,  15,  12,
    9,   7,   5,   4,   3,   2,   1,   0
};

// duration helpers
#define DURATION_1HR   3600000
#define DURATION_2HR   7200000
#define DURATION_3HR  10800000

// servo pulse control
#define SERVO_MIN_US 1000
#define SERVO_MAX_US 2000
#define SERVO_REFRESH_MS 20

#define SERVO_DELTA_US (SERVO_MAX_US - SERVO_MIN_US)

// feed rates
#define ROT_NEUTRAL  90
#define ROT_FORWARD  (ROT_NEUTRAL + 20)
#define ROT_REVERSE  (ROT_NEUTRAL - 20)

// feed control
#define FEED_INTERVAL_MS  DURATION_3HR
#define FEED_COUNT        2
#define FEED_FORWARD_MS   1500
#define FEED_REVERSE_MS    500

// debouncer
#define DEBOUNCE_WAIT_MS 5



boolean firstTime = true;
int lastButtonState = HIGH;

unsigned long lastFeedTime = 0;
unsigned long lastDebounceTime = 0;

void runServo(unsigned int angle, unsigned int duration)
{
  unsigned long timeOn = SERVO_MIN_US + ((unsigned long)SERVO_DELTA_US * angle) / 180;
  unsigned long timeOff = (SERVO_REFRESH_MS * 1000) - timeOn;
  unsigned int offMs = timeOff / 1000;
  unsigned int offUs = timeOff % 1000;
  
  for (unsigned int ct = 0; ct < duration; ct += SERVO_REFRESH_MS)
  {
    digitalWrite(PIN_SRV, HIGH);
    delayMicroseconds(timeOn);
    digitalWrite(PIN_SRV, LOW);
    delayMicroseconds(offUs);
    delay(offMs);
  }
}

void setup()
{
  pinMode(PIN_BTN, INPUT);
  pinMode(PIN_LED, OUTPUT);
  pinMode(PIN_SRV, OUTPUT);
  
  digitalWrite(PIN_LED, LOW);
  digitalWrite(PIN_SRV, LOW);
}

void loop()
{
  boolean triggerFeed = false;
  unsigned long timeNow = millis();

  //
  // detect if button is pressed (with debounce), where we trigger
  //

  // read the current state for manual debounce
  int currentButtonState = digitalRead(PIN_BTN);
  if (currentButtonState != lastButtonState)
  {
    lastDebounceTime = timeNow;
    lastButtonState = currentButtonState;
  }
  // and figure out if it's been long enough
  if ((timeNow - lastDebounceTime) > DEBOUNCE_WAIT_MS)
  {
    // feed with a LOW signal
    if (currentButtonState == LOW)
    {
      triggerFeed = true;
    }
  }

  //
  // check if we met the feed interval
  //

  if ((timeNow - lastFeedTime) >= FEED_INTERVAL_MS)
  {
    lastFeedTime = timeNow;
    triggerFeed = true;
  }

  //
  // if we've just powered on, do a feeding
  //

  if (firstTime)
  {
    firstTime = false;
    triggerFeed = true;
  }

  //
  // dim the LED from bright (just fed) to off (feed soon)
  //

  // convert to a 5-bit value for the brightness table
  unsigned long scaling = FEED_INTERVAL_MS / 31;
  int ledValue = (timeNow - lastFeedTime) / scaling;
  // write the LED signal
  analogWrite(PIN_LED, pgm_read_byte(&brightness[ledValue])); 

  //
  // trigger a feeding
  //

  if (triggerFeed)
  {
    lastFeedTime = timeNow;

    digitalWrite(PIN_LED, HIGH);
    for (int count = 0; count < FEED_COUNT; count++)
    {
      runServo(ROT_FORWARD, FEED_FORWARD_MS);
      digitalWrite(PIN_LED, LOW);
      runServo(ROT_REVERSE, FEED_REVERSE_MS);
      digitalWrite(PIN_LED, HIGH);
      runServo(ROT_FORWARD, FEED_REVERSE_MS);
    }
    digitalWrite(PIN_LED, LOW);
  }
}

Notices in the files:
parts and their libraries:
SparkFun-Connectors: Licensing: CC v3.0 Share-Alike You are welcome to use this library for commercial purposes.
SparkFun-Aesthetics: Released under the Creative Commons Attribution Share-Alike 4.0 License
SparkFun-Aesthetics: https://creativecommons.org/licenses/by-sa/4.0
